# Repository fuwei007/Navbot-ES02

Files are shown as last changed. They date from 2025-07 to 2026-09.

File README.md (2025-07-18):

# Navbot-ES02 - Open Source Desktop Dual-Wheel Legged Robot

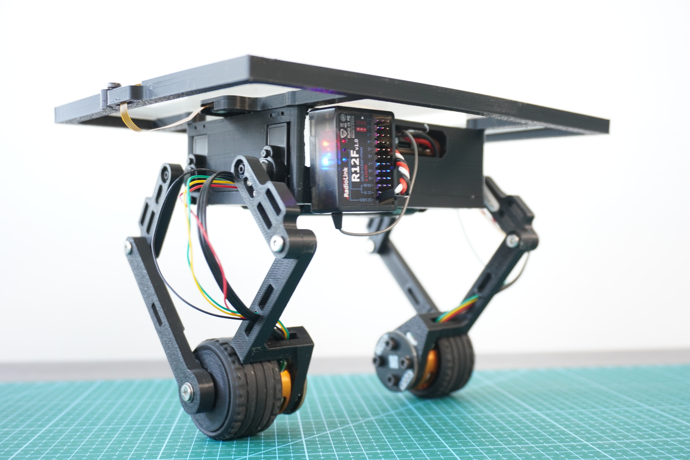
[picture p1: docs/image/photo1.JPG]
robot


**Navbot-ES02** is a compact, open-source desktop robot that combines self-balancing wheels with articulated legs. It’s an experimental platform for exploring locomotion, balance, and user interaction — ideal for makers, educators, and robotics enthusiasts.

Full tutorial: [Frank Fu’s Build Guide](https://frankfu.blog/embodied-ai-robot/diy-desktop-dual-wheel-legged-roboy/)

---

##  Key Features

-  **Self-balancing** using MPU6050 and PID control
-  **Legged motion** using 270° digital servos
-  **Touchscreen interface** for motion control to achieve  ball-balancing
-  **Radiolink T12D RC System** for real-time operation switching via PWM/SBUS.
-  **Modular Arduino-based firmware** for easy customization

---

## Hardware Overview

| Component | Description |
|---|---|
| **MCU** | ESP32-S3 DevKit |
| **Motors** |  2208 90KV 3mm Shaft Gimbal Brushless Motors |
| **IMU** |  ICM42688 a 3-axis gyroscope and a 3-axis accelerometer |
| **Servos** | Pro-Tronik PTK 7452 MG-D 2.8kg/0.11s 12.3g Micro Digital Servo |
| **HMI** | 2.8" resistive/capacitive touchscreen |
| **Battery** | 2Pcs 18650 Battery Charger Pack |
| **Controller** | Radiolink T12D 12CH 2.4G RC Transmitter R12F Receiver |

---

## 📦 Software Structure

```
Navbot-ES02/
├── OllieFOCdrive/     # Motor & balance control
├── TouchUI/           # Touchscreen-based user interface
├── WiFiControl/       # Optional WebSocket/HTML control panel
├── partitions.csv     # Flash partition layout
└── lib/               # Required Arduino libraries
```

---

## Getting Started

### 1. Install Requirements

- Arduino IDE 2.x
- ESP32 board package (`esp32@3.0.7`)
- Libraries (via Library Manager or GitHub):
  - [SimpleFOC](https://github.com/simplefoc/Arduino-FOC)
  - [SimpleFOcDrivers](https://github.com/simplefoc/Arduino-FOC-drivers)
  - [Preferences](https://github.com/vshymanskyy/Preferences)
    
### 2. Flash the Firmware

```bash
git clone https://github.com/fuwei007/Navbot-ES02.git
```

- Open `OllieFOCdrive.ino` with Arduino IDE
- Select board: `ESP32S3 Dev Module`
- Upload code and monitor via Serial for debugging

### 3. Connect the model remote control
ES02 has 3 lines, namely GND, 5V, and sbus.

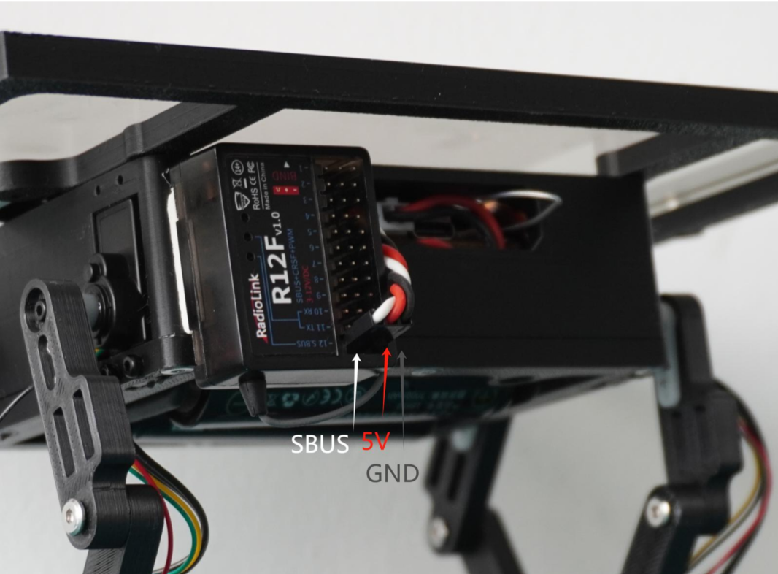
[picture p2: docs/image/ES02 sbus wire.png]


The remote control receiver may have multiple interfaces. It is necessary to confirm the sbus
output port by yourself. The following picture shows the wiring ports of the RadioLink receiver.

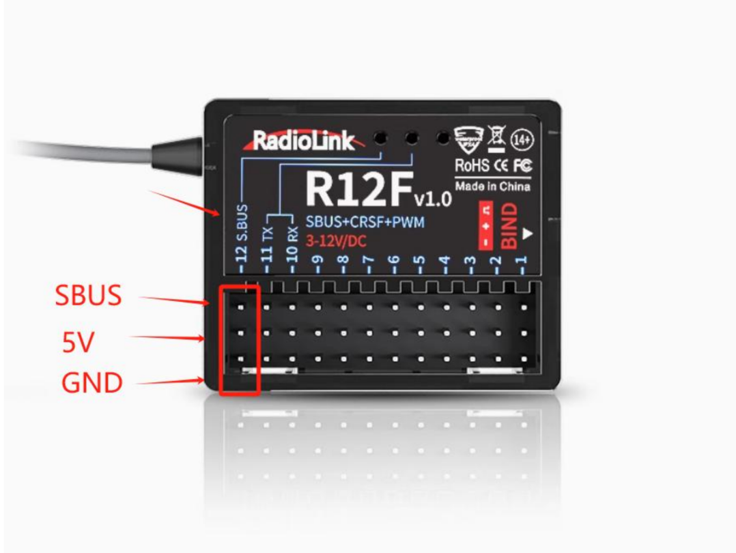
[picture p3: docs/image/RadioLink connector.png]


The channels of the joystick are generally defaulted to ch1-4. Besides, six auxiliary channels
are needed to switch on some functions. Each remote control is different, and they should be set
according to personal habits. The corresponding functions of ch6-10 can be referred to as follows:

- CH5 : 3-section switch, 0:stop, 1:start, 2:start and touch tablet enable. 
- CH6 : 2-section switch, 0:posture mode, 1:mark mode. 
- CH7 : 2-section switch, manual or auto roll, 0:manual , 1:auto . 
- CH8 : 3-section switch, 0:default, 1:pitching adjust, 2:ball poise. 
- CH9 : The x-coordinate of the small ball . 
- CH10:The y-coordinate of the small ball.

---

## Tourial Videos

- DIY ES02 Desktop dual-wheel legged bot Preview:
  
  Video 2 (https://www.youtube.com/watch?v=u7Jmyq_AXwc)

- Open Source ESP32 DIY Robot ES02: Learn Coding & Robotics | Educational Dual-Wheel Legged Bot:
  Video 1 (https://www.youtube.com/watch?v=hujr_VRSyrw)

---

## Discord link
| Link: [https://discord.gg/syywQ2CKN3](https://discord.gg/syywQ2CKN3)        |
| :------------: |
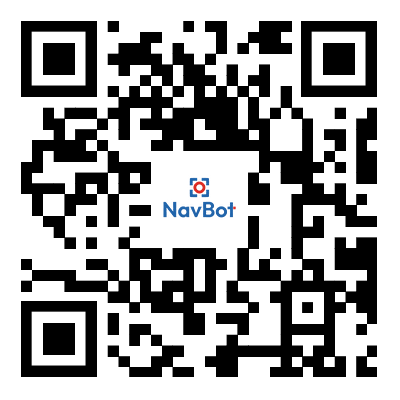
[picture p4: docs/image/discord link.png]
|  |

---

## Acknowledgments

- [SimpleFOC Community](https://simplefoc.com/)
- [Frank Fu’s Robotics Blog](https://frankfu.blog)
- [LVGL GUI Library](https://lvgl.io/)
- Arduino & ESP32 Open Source Communities

---

> Feel free to fork, contribute, or build your own version!  
> PRs and feedback are always welcome.

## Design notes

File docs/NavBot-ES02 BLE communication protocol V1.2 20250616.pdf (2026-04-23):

# NAVBOT-ES02 BLE communication protocol

Table of Contents

## Revision History

# DOCUMENT HISTORY

SOFTWARE REVISION | CHANGES MADE | REVISION DATE | EDITED BY
1.0 | First draft | 6/12/2025 | XiaoleChen
1.1 | Modify the description of the 12th byte in CMD_MANEUVER | 6/16/2025 | XiaoleChen
1.2 | Add the JSON protocol and define the key name:get_device_info | 3/30/2026 | XioaleChen

## 1. BLE information

BLE NAME :
navbot_es02-******

Service UUID:
6E400011-B5A3-F393-E0A9-E50E24DCCA9E

Send data characteristic UUID: 6E400012-B5A3-F393-E0A9-E50E24DCCA9E

Receive data characteristic UUID: 6E400013-B5A3-F393-E0A9-E50E24DCCA9E

## 2. Data frame agreement

Byte | Name | Description
Byte 1 | Header1 | Fixed 0x55
Byte 2 | Header2 | Fixed 0xAA
Byte 3 | Command | The control command of this data frame, reference 3.Command
Byte 4 | Remaining | The number of frames remaining after synthesizing the complete data,reference 4.Subcontracting
Byte 5 | Null | Retain
Byte 6 | Data
Byte 7 | Data
Byte 8 | Data
Byte 9 | Data
Byte 10 | Data
Byte 11 | Data
Byte 12 | Data
Byte 13 | Data
Byte 14 | Data
Byte 15 | Data
Byte 16 | Data
Byte 17 | Data
Byte 18 | Data
Byte 19 | Data
Byte 20 | Data

## 3. Command

The third byte is the command byte, which determines the function of the data from the 6th to the 20th byte. The current definition is as follows:
Command | Name | Explanation
0x10 | CMD_MANEUVER retain | Robot maneuver, at this time the meaning of the data frame reference 3.0.CMD_MANEUVER. 0x01
0x02 | CMD_JSON

JSON transmission, byte 6 to byte 20 represent the JSON body. Refer to 3.2. CMD_JSON

## 3.0. CMD_MANEUVER

When byte3(command) is equal to 0x00, it indicates that bytes 6 to 20 control the maneuverability of the robot. At this time, the data should follow the following rules:
Byte | Name | Description
Byte 1 | Header1 | Fixed 0x55
Byte 2 | Header2 | Fixed 0xAA
Byte 3 | Command | 0x10
Byte 4 | Remaining | 0x00
Byte 5 | Null | 0x00
Byte 6 | CH1_roll | The robot leans to the left and right. Value 100 to -100. Byte 7 | CH2_height | The height of the robot. Value 0 to 100 . Byte 8 | CH3_pitching | Move forward or backward. Value 100 to -100. Byte 9 | Ch4_yaw | The robot spin. Value 100 to -100. Byte 10 | SWA_en | 3-section switch, 0:stop, 1:start, 2:start and touch tablet
enable. Byte 11 | SWB_posture | 2-section switch, 0:posture mode, 1:mark mode. Byte 12 | SWC_roll_mode | 2-section switch, manual or auto roll, 0:manual , 1:auto . Byte 13 | SWD_posture_option | 3-section switch, 0:default, 1:pitching adjust, 2:ball poise. Byte 14 | VRA_ball_x | The x-coordinate of the small ball. Value 5 to -5. Byte 15 | VRB_ball_y | The y-coordinate of the small ball. Value 5 to -5. Byte 16 | Null | 0x00
Byte 17 | Null | 0x00
Byte 18 | Null | 0x00
Byte 19 | Null | 0x00
Byte 20 | Null | 0x00

## 3.0.1. Data frame demonstration：

55 AA 10 00 00 00 00 00 00 01 00 00 00 00 00 00 00 00 00 00
SWA_en(Byte 10) = 1, At this point, start the machine and hold it upright with your hand. Then you can stand still on the

spot. 55 AA 10 00 00 00 00 0A 00 01 00 00 00 00 00 00 00 00 00 00

SWA_en(Byte 10) | = 1, CH3_pitching(Byte 8) = 10, After standing up, the machine moved forward at a speed of 10. 55 AA 10 00 00 00 00 8A 00 01 00 00 00 00 00 00 00 00 00 00
SWA_en(Byte 10) | = 1, CH3_pitching(Byte 8) = -10, After standing up, the machine moves backward at a speed of 10. 55 AA 10 00 00 00 00 00 08 01 00 00 00 00 00 00 00 00 00 00
SWA_en(Byte 10) | = 1, Ch4_yaw(Byte 9) | = 8, After standing up, the machine rotates clockwise at an angular velocity of 8. 55 AA 10 00 00 00 00 00 88 01 00 00 00 00 00 00 00 00 00 00
SWA_en(Byte 10) | = 1, Ch4_yaw(Byte 9) | = -8, After standing up, the machine rotates counterclockwise at an angular velocity of 8. 3.1. NULL

## 3.2. CMD_JSON:

This command data frame format is:
Byte | Name | Description
Byte 1 | Header1 | Fixed 0x55
Byte 2 | Header2 | Fixed 0xAA
Byte 3 | Command | 0x02

Byte 4 | Remaining Null | * Byte 5 Idle

Byte 6 ~Byte 20
Body data JSON body,Transmission can be subcontracted. 3.2.1. JSON protocol :

Using the key name "type" to distinguish different commands, the currently defined values for the "type" key are as follows:
Type value：(string) | explain
“get_device_info” | Obtain robot information, refer to 3.2.1.1 get_device_info

## 3.2.1.1. get_device_info

The upper computer sends:
{ “type”:”get_device_info”

}
Robot reply:
{ | “type”: | “get_device_info”, “battery_level”: | double, “battery_voltage”: double, }

## 4. Subcontracting

The number of frames remaining after synthesizing the complete data;The size of one frame of data is 20 bytes. Excluding the 5-byte header, the user can still use 15 bytes. However, when using commands such as JSON, these 15 bytes are clearly insufficient for use. Therefore, the 4th byte of each frame data can be used to indicate how many more frames of data are to

be processed together. For example, if the data to be sent now consists of 32 bytes, the data format would be as follows (xx represents the actual data):

### 55 AA xx 02 00 xx xx xx xx xx xx xx xx xx xx xx xx xx xx xx 55 AA xx 01 00 xx xx xx xx xx xx xx xx xx xx xx xx xx xx xx 55 AA xx 00 00 xx xx xx xx xx xx xx xx xx xx xx xx xx xx xx

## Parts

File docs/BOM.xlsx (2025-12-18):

Category | Component | linkS | Specification | Quantity | Description
Hardware | Flanged Bearing | https://www.amazon.com/XIKE-Bearings-3x6x2-5mm-Pre-Lubricated-Selectric/dp/B0D2KYP9JD | 3×6×2.5 mm | 2 | Rod L2
 | Bearing | https://www.amazon.com/uxcell-6701-2RS-Groove-Bearings-Double/dp/B082PQ8DC2 | 12×18×4 mm | 2 | Wheel Hub
 | Hex Socket Screw | https://www.amazon.com/Fgruh-750PCS-Assortment-Washers-Assorted/dp/B0FGV5FCBN?sp_csd=d2lkZ2V0TmFtZT1zcF9hdGY | M3×6 | 2 | Wheel Hub to Rod L2
 | Hex Socket Screw |  | M3×10 | 8 | Motor to Encoder
 | Hex Socket Screw | https://www.amazon.com/Fgruh-1200PCS-Assortment-Washers-Assorted/dp/B0FGV5K8BT?sp_csd=d2lkZ2V0TmFtZT1zcF9hdGY | M2×8 | 4 | Servo to Servo Arm
 | Hex Socket Screw |  | M2×6 | 6 | Wheel Hub to Motor
 | Hex Locking Screw & Nut | https://detail.tmall.com/item.htm?ali_trackid=318_23a26b5b4c76f7f8a2ef9837f0edb194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 | M2×12 (Set) | 8 | Lower Arm to Upper Arm
 | Hex Socket Self-tapping Screw | https://www.amazon.com/Metric-Tapping-Stainless-Assortment-Drilling/dp/B0D1R21JRR | M3×5 | 6 | Mainboard to Bracket ×4 / Touchscreen to Stand ×2
 | Countersunk Hex Self-tapping Screw |  | M3×6 | 2 | Battery Holder
 | Countersunk Hex Self-tapping Screw |  | M3×10 | 12 | Base to Bracket ×4 / Base to Top Cover ×4 / Top Cover to Touchscreen Stand ×4
 | Countersunk Hex Self-tapping Screw |  | M3×18 | 12 | Rod L5 / Rod L6
 | Hex Socket Self-tapping Screw | https://www.amazon.com/Whitewashed-Self-Tapping-Hexagonal-Self-Drilling-Fasteners/dp/B0F1JYTY33 | M1.7×6 | 8 | Servo Arm to Rod L1
 | Hex Socket Self-tapping Screw | https://www.amazon.com/Whitewashed-Self-Tapping-Hexagonal-Self-Drilling-Fasteners/dp/B0F1JYKM64 | M1.7×10 | 8 | Servo to Base
 | Steel Ball (Diameter) | // | 22 mm | 1 | Used for top ball support
Wires | SH1.0 Cable | jLhkiMjvlWzf20CDxy2JfJ4Jcx6Da1d6_YxCGVCAp2FeKimA2qR2AeveBVZlwNlAqCN59ZZSTGm0iPQm9QxrrhbzW8yj_p5FoFC0xtJEouJcRDbRKffhAhPzKMzW5XBSkb6nk7JZq8_URwwl9zUZRra7onyzfd1nP7ulprgyJr7Y40WYrsKdRTsBeodiVKbwYnfKO1gHhlIl8zZwIQNvCrqvjZLzNFy9HY3i_j13vM2EiAD5jhJBrvSYUlat2Xb1bodeY7x2JP6XTelKuG9nJ0bqOmzMA | 200 mm, reverse connection | 3 | 2 Encoders / Communication between two units
 | SH1.0 Cable |  | 100 mm, reverse connection | 1 | Touchscreen control board to mainboard
 | Dupont Cable | https://www.amazon.com/Kidisoii-Dupont-Connector-Pre-Crimped-3P-30CM/dp/B0CCTXZW3D | 3PIN × 10 cm | 1 | To SUBS receiver
Electronics | Encoder Module | // | AS5600 | 2
 | Mini quadruped mainboard | // |  | 1
 | Resistive Touchscreen | https://item.taobao.com/item.htm?app=chrome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 | 181×139 mm | 1
 | 4-wire Resistive Touchscreen Driver | // | Serial TTL level | 1
 | ICM42688P Module | // |  | 1
 | Tire Rubber | https://www.amazon.com/Shaluoman-Soft-Rubber-Tires-Tyre/dp/B07F8Q4BHJ | 37×22 mm (outer diameter × width) | 2
 | Servo | https://item.taobao.com/item.htm?id=534087183869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 | GX-S7445 | 4
 | Brushless Motor | https://www.amazon.com/Gimbal-Brushless-100-200g-Gopro3-Quadcopter/dp/B0FM8JYT38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 | 2208-90kv | 2
 | 18650 Battery Holder | https://www.amazon.com/DAIERTEK-18650-Battery-Holder-Total/dp/B0BG3YLCFD?sp_csd=d2lkZ2V0TmFtZT1zcF9hdGY | 2S battery holder | 1
 | Radial Magnet | https://www.amazon.com/GXHUANG-6x1-5mm-Decorative-Refrigerator-Projects/dp/B0DHQ7FY14 | 6×1.5 mm | 2
 | Remote + Receiver Set | https://www.amazon.com/Radiolink-T12D-Transmitter-Telemetry-Long-Range/dp/B0DB5JHSS6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 | T12D | 1 | Ten control channels are required.
 | 18650 Battery | https://www.amazon.com/MC-ELIN-Rechargeable-Batteries-Flashlights-Headlamps/dp/B0FSQT6BMF |  | 2
3D Printed Parts | loamcake |  |  | 1 | Top Cover
 | lowercover |  |  | 1 | Base
 | magnetsleeve |  |  | 2 | Magnet Sleeve
 | motherboardbracket |  |  | 1 | Mainboard Bracket
 | pole1 |  |  | 2 | Rod L1
 | pole2 |  |  | 2 | Rod L1
 | pole3 |  |  | 2 | Rod L2
 | pole4 |  |  | 2 | Rod L2
 | pole5 |  |  | 2 | Rod L5 (for two-unit connection)
 | pole6 |  |  | 2 | Rod L6 (for two-unit connection)
 | wheelHub |  |  | 2 | Wheel Hub
 | touchscreenstand |  |  | 1 | Touchscreen Bracket

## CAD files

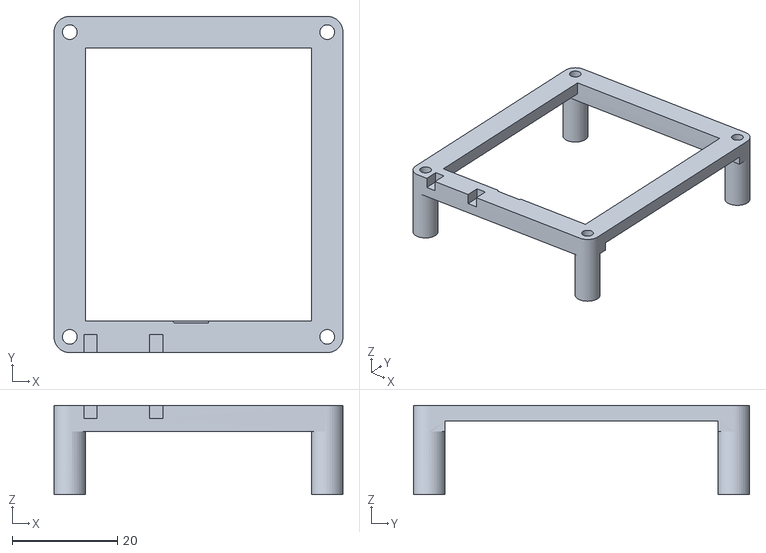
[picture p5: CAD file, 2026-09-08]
hardware/3d print/motherboardbracket_hollow.stl
55.0 x 64.0 x 17.0

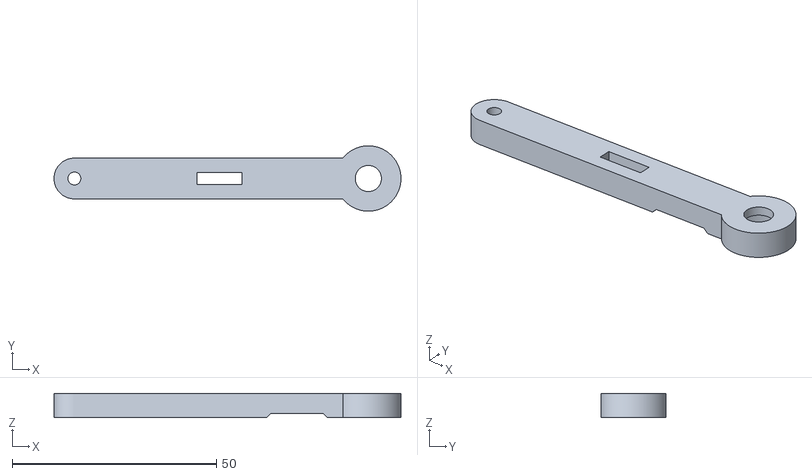
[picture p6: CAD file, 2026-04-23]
hardware/3d print/Calf_Outside.stl
85.0 x 16.0 x 6.00

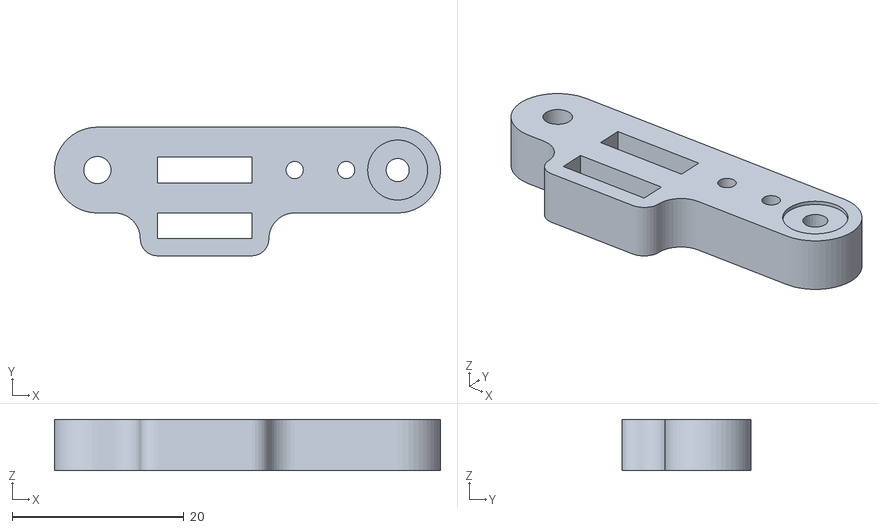
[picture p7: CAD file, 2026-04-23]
hardware/3d print/Thigh_R.stl
45.0 x 15.0 x 6.00

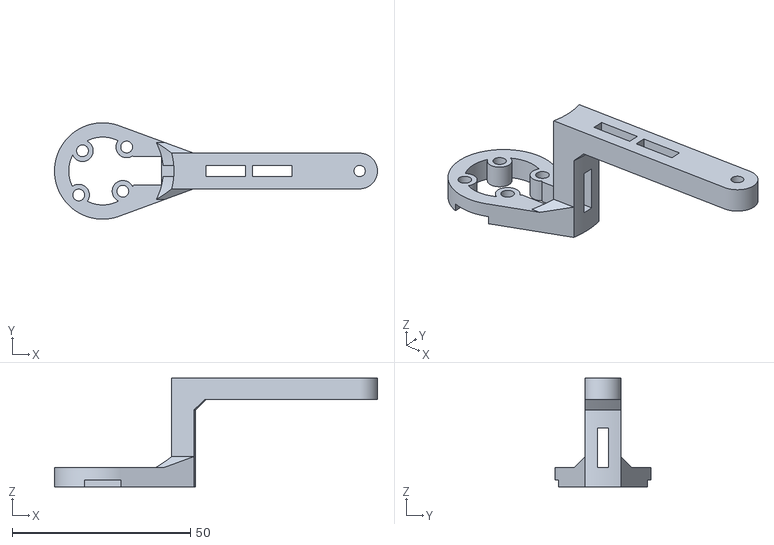
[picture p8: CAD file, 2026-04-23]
hardware/3d print/Calf_Inside.stl
90.5 x 27.0 x 30.5

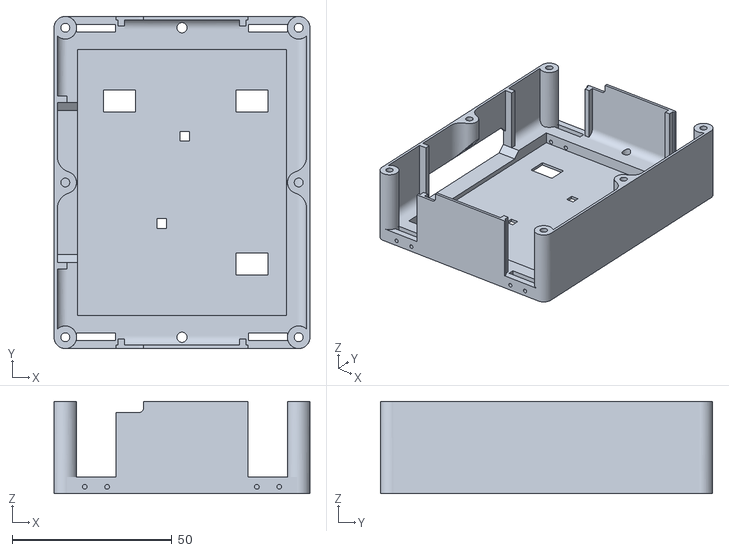
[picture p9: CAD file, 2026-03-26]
hardware/3d print/loamcake.stl
80.1 x 103.9 x 28.8

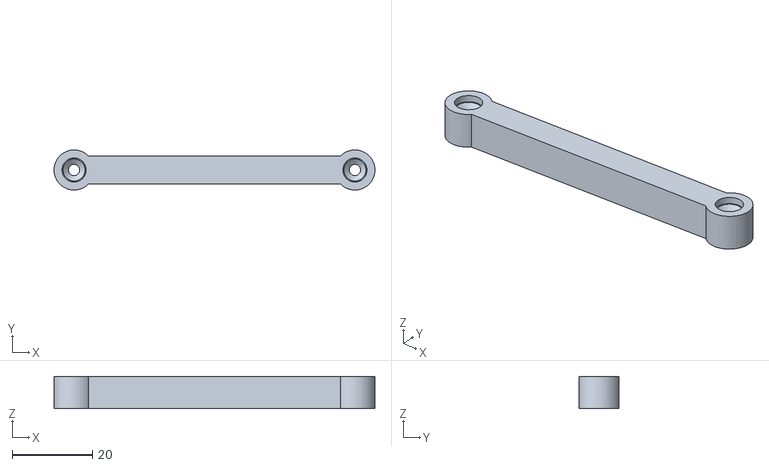
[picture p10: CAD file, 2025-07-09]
hardware/3d print/pole6.stl
80.0 x 9.99 x 8.00

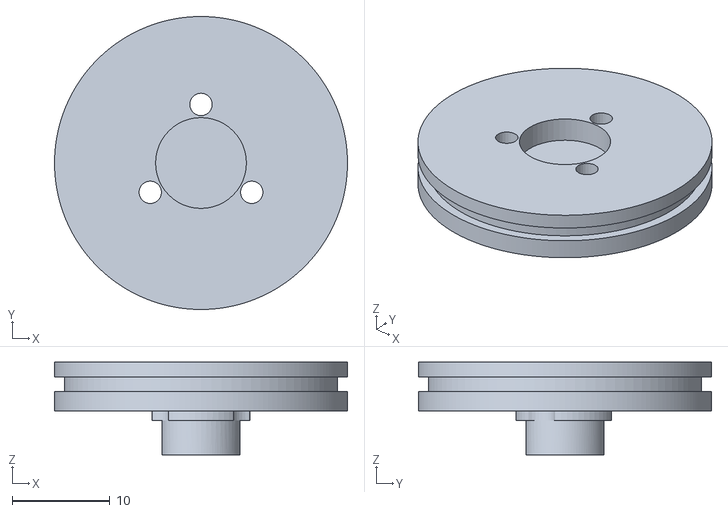
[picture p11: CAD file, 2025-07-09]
hardware/3d print/Wheel_Hub.stl
30.0 x 30.0 x 9.50

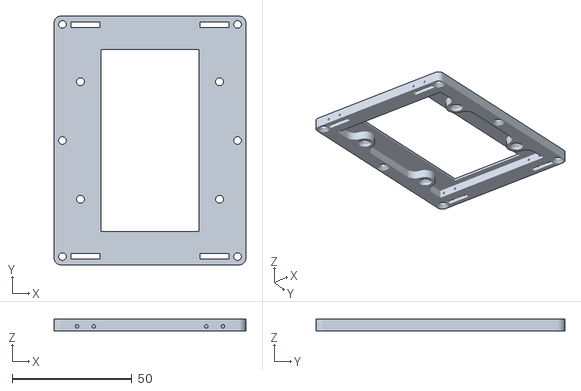
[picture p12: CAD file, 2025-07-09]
hardware/3d print/lowercover.stl
80.0 x 103.8 x 5.00

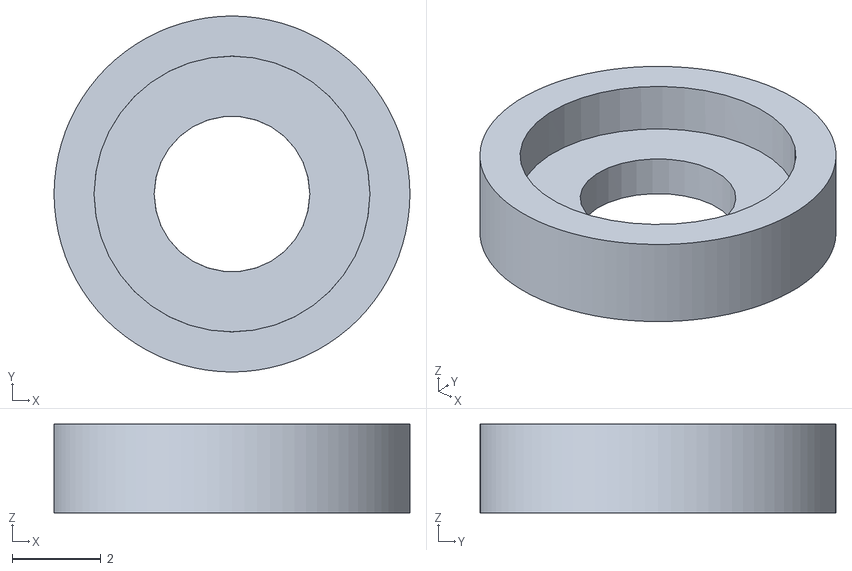
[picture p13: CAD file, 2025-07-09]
hardware/3d print/magnetsleeve.stl
8.00 x 8.00 x 2.00

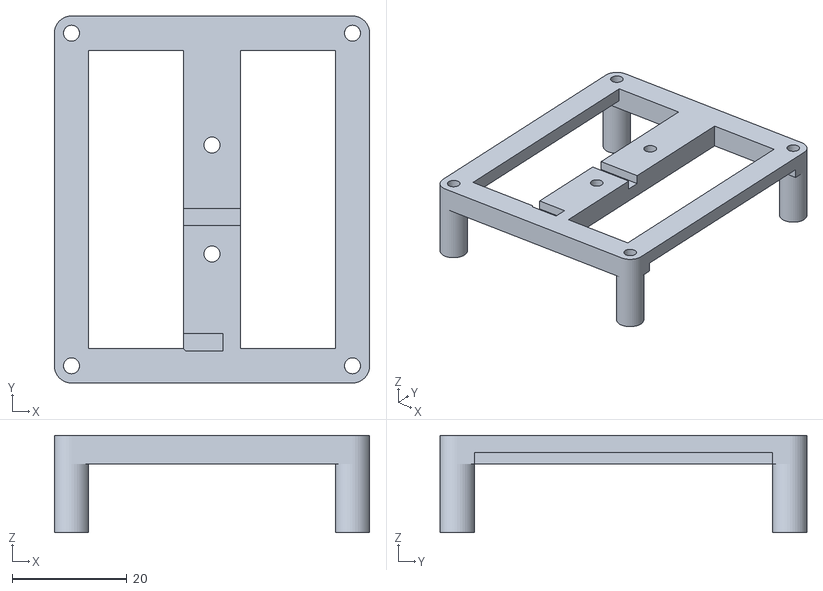
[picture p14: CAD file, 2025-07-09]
hardware/3d print/motherboardbracket.stl
55.0 x 64.0 x 17.0

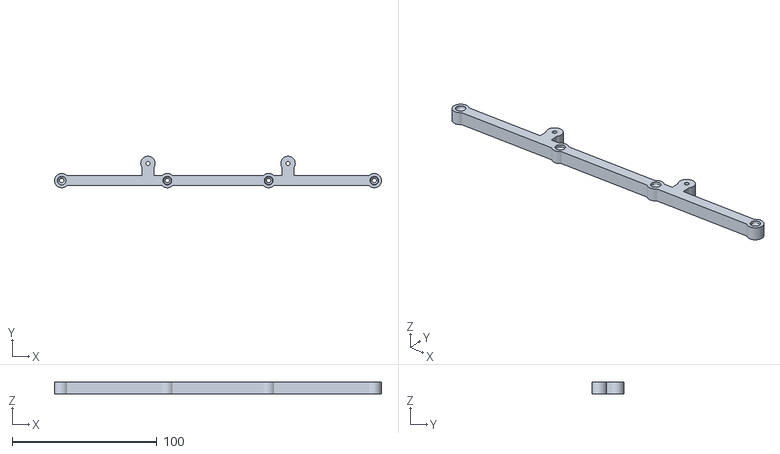
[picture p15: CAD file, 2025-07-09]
hardware/3d print/pole5.stl
226.0 x 21.9 x 8.00

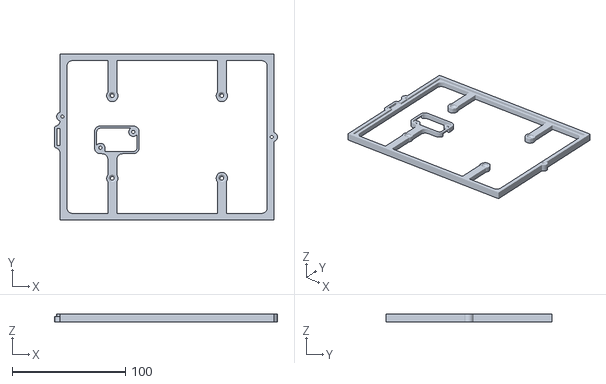
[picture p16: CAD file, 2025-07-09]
hardware/3d print/touchscreenstand.stl
197.1 x 147.0 x 7.00

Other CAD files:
hardware/3d print/Thigh_L.stl

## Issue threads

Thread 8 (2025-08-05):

Temperature collection anomaly

nullhat2, 2025-08-05:
The temperature collection method is abnormal, resulting in compilation failure.

Closed 2025-08-08.

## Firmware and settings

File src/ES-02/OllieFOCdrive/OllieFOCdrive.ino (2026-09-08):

#include <Arduino.h>
#include <SimpleFOC.h>
#include <Preferences.h>  // This library is used for key-value data storage and retrieval in ESP32, enabling data persistence
#include "SlotCalibration.h"
#include "FUTABA_SBUS.h"
#include "ServoControl.h"
#include "ICM42688.h"
#include "MahonyFilter.h"
#include "OllieFOCdrive.h"
#include "filter.h"
#include "touchscreen.h"
#include "ble.h"
#include "robot.h"


// commander communication instance
Commander command = Commander(Serial);

// ----- Editable Constants
#define SensorSwitch SENSOR_SWITCH_IIC_AS5600                                // 1: SPI  2: IIC AS5600
#define Communication_object COMMUNICATION_OBJECT_TWO_OR_FOUR_WHEEL_BALANCE  // 0: 2-wheel balance || 4-wheel balance movement  1: simpleFOC Studio host computer  2: control dual motors  3: sample torque data
#define TorqueCompensation TORQUE_COMPENSATION_OFF                           // 1: torque compensation  0: no torque compensation (cannot be modified)
#define SwitchUser SWITCH_USER_MODE_SPEED_MODE                               // 0: view encoder position and direction  1: sample motor 1 torque compensation data  2: sample motor 2 torque compensation data  3: torque  4: speed  5: angle mode
#define CurrentUser CURRENT_LOOP_OFF                                         // 1: enable current loop
#define M2CurrentUser CURRENT_LOOP_OFF                                       // 1: enable current loop for motor 2

#define AdjusParameter ADJUST_BALANCE_SPEED_YAW_ROLL        // 0: balance, speed, yaw, roll parameter tuning   1: ball pushing
#define SwitchingPattern SWITCHING_PATTERN_TWO_WHEEL_MODE   // 0: two-wheel  1: four-wheel  switching mode
#define MasterSlaveSelection MASTER_SLAVE_SELECTION_MASTER  // 0: slave   1: master

//      Two-Wheel PID Gains for Remote Control Mode (Without Touchscreen)
#define PID_ROLL_P_NO_TOUCH 0.06
#define PID_ROLL_I_NO_TOUCH 1.5
#define PID_ROLL_D_NO_TOUCH 0.0028
#define PID_ROLL_LIMIT_NO_TOUCH 2
#define PID_SPEED_P_NO_TOUCH 0.3
#define PID_SPEED_I_NO_TOUCH 0.3
#define PID_SPEED_D_NO_TOUCH 0
#define PID_SPEED_LIMIT_NO_TOUCH 50
#define PID_ANGLE_P_NO_TOUCH 66
#define PID_ANGLE_I_NO_TOUCH 222  // if stuttering/shaking when balancing, consider reducing this Integral value (ex. 165 instead of 222)
#define PID_ANGLE_D_NO_TOUCH 1
#define PID_ANGLE_LIMIT_NO_TOUCH 0.1

//      Two-Wheel PID Gains for Remote Control Mode (With Touchscreen)
#define PID_ROLL_P_WITH_TOUCH 0.08
#define PID_ROLL_I_WITH_TOUCH 1.5
#define PID_ROLL_D_WITH_TOUCH 0.005
#define PID_ROLL_LIMIT_WITH_TOUCH 2
#define PID_SPEED_P_WITH_TOUCH 0.12
#define PID_SPEED_I_WITH_TOUCH 0.12
#define PID_SPEED_D_WITH_TOUCH 0
#define PID_SPEED_LIMIT_WITH_TOUCH 50
#define PID_ANGLE_P_WITH_TOUCH 9
#define PID_ANGLE_I_WITH_TOUCH 222
#define PID_ANGLE_D_WITH_TOUCH 0.11
#define PID_ANGLE_LIMIT_WITH_TOUCH 0.1

#define IMU_SAMPLING_RATE_HZ 1000.0f  // Sampling frequency
#define IMU_LPF_CUTOFF_FREQ_HZ 50.0f  // Cutoff frequency for low-pass filter
#define IMU_CALL_COUNT 100            // Number of times the function is called

#define BODY_THIGH_LENGTH_M 0.035f  // Thigh length (m)
#define BODY_SHANK_LENGTH_M 0.072f  // Shank length (m)

#define BOARD_PIN_LED 35        // LED IO
#define BOARD_PIN_ANALOG_IN 17  // Battery voltage IO

#define IMU_ACCEL_RANGE_G 8.0              // Unit: g
#define IMU_GYRO_RANGE_DEG_PER_SEC 2000.0  // Unit: °/s

#define CUSTOM_SERVO_1_PIN 11
#define CUSTOM_SERVO_2_PIN 12
#define CUSTOM_SERVO_3_PIN 21
#define CUSTOM_SERVO_4_PIN 14

#define CURRENT_SENSOR_MV_PER_AMP 90.0f  // ACS712-05B sensitivity is 185mV/A

#define SBUS_CHANNEL_MAX 1792
#define SBUS_CHANNEL_MIN 192

#define SERIAL_PACKET_HEADER_BYTE_1 12
#define SERIAL_PACKET_HEADER_BYTE_2 34
#define SERIAL_PACKET_END_BYTE 0
#define SERIAL_BAUD_RATE 2000000
// -------------------------------------

// Body
float TargetLegLength = 0;          // Target leg length
float LegLength = 0.06f;            // Leg length
float BarycenterX = 0;              // Center of mass X
float BodyPitching = 0;             // Pitch
float BodyRoll = 0;                 // Roll
float MovementSpeed = 0;            // Movement speed
float BodyTurn = 0;                 // Turning
float SlideStep = 0;                // Slide step
float BodyX = 0;                    // X position (controller output)
int RobotTumble = ROBOT_TUMBLE_NO;  // Robot tumble (fall detection)

body_t body;

// 滤波
float LegLength_f = 0.06f;     // Leg length
float BarycenterX_f = 0;       // Center of mass X
float BodyPitching_f = 0;      // Pitch
float BodyRoll_f = 0;          // Roll
float MovementSpeed_f = 0;     // Movement speed
float BodyTurn_f = 0;          // Turning
float SlideStep_f = 0;         // Slide step
float BodyX_f = 0;             // X position
biquadFilter_t FilterLPF[15];  // Second-order low-pass filter
float TouchY_Pid_outputF = 0;
float TouchX_Pid_outputF = 0;

float cutoffFreq = 200;
float enableDFilter = 1;
float LpfOut[6];  //

void CutoffFreq(char *cmd) {
  command.scalar(&cutoffFreq, cmd);
}

void EnableDFilter(char *cmd) {
  command.scalar(&enableDFilter, cmd);
}

int LED_HL = 1;
int LED_count = 0;
int LED_dt = 100;
int sensorValue = 0;              // value read from the pot
biquadFilter_t VoltageFilterLPF;  // Second-order low-pass filter
uint16_t VoltageADC = 0;          // Battery voltage ADC data
float VoltageADCf = 0;            // Battery voltage ADC data
float Voltage = 0;                // Battery voltage

// IMU
//  Create MahonyFilter object, set proportional gain and integral gain
MahonyFilter mahonyFilter(0.4f, 0.001f);
// Accelerometer range (here set to ±8g)
// Gyroscope range (here assumed to be ±2000°/s)
attitude_t attitude;
float roll_ok;   //
float pitch_ok;  //

zeroBias_t zeroBias;  // Zero offset
unsigned long timestamp_prev = 0;
float IMUtime_dt = 0;

/* Low-pass filter parameters */
float RATE_HZ_last = IMU_SAMPLING_RATE_HZ;            // Sampling frequency
float LPF_CUTOFF_FREQ_last = IMU_LPF_CUTOFF_FREQ_HZ;  // Cutoff frequency

float RATE_HZ = IMU_SAMPLING_RATE_HZ;            // Sampling frequency
float LPF_CUTOFF_FREQ = IMU_LPF_CUTOFF_FREQ_HZ;  // Cutoff frequency
biquadFilter_t ImuFilterLPF[6];                  // Second-order low-pass filter

void ImuRATE_HZ(char *cmd) {
  command.scalar(&RATE_HZ, cmd);
}
void ImuLPF_CUTOFF_FREQ(char *cmd) {
  command.scalar(&LPF_CUTOFF_FREQ, cmd);
}

void Target_Leg_Length(char *cmd) {
  command.scalar(&TargetLegLength, cmd);
}

// Complementary filter
float angleGyroX, angleGyroY, angleGyroZ,
  angleAccX, angleAccY;
float angleX, angleY, angleZ;
float accCoef = 0.02f;
float gyroCoef = 0.98f;

//  Declare a Preferences object for subsequent read/write operations to flash memory
Preferences preferences;
//  Define a floating-point array to store Euler angle data
float zeroBiasFlash[9];
//  Define a character string pointer array to store the keys corresponding to the roll and pitch angles, which can be directly modified by the user
//  The key name is used to uniquely identify data in flash memory
const char *zeroBiasKeys[9] = {
  "roll",
  "pitch",
  "gyroX",
  "gyroY",
  "gyroZ",
  "servoAngle1",
  "servoAngle2",
  "servoAngle3",
  "servoAngle4"
};

int IMUCallCounter = 0;  //  Call counter

// Servo
void zeroBias_servo1(char *cmd) {
  command.scalar(&zeroBias.servo1, cmd);
}
void zeroBias_servo2(char *cmd) {
  command.scalar(&zeroBias.servo2, cmd);
}
void zeroBias_servo3(char *cmd) {
  command.scalar(&zeroBias.servo3, cmd);
}
void zeroBias_servo4(char *cmd) {
  command.scalar(&zeroBias.servo4, cmd);
}

bool pid_gains_mode_is_enabled(int mode) {
  return (mode == REMOTE_CONTROL_PID_GAINS_MODE_ON_WITHOUT_TOUCH || mode == REMOTE_CONTROL_PID_GAINS_MODE_ON_WITH_TOUCH);
}

//  Create ServoControl object, pass in the custom pin
ServoControl servoControl(CUSTOM_SERVO_1_PIN, CUSTOM_SERVO_2_PIN, CUSTOM_SERVO_3_PIN, CUSTOM_SERVO_4_PIN);

// Remote control
FUTABA_SBUS sBus;
float sbuschx[8] = { 0 };
int sbus_dt_ms = 0;
int pid_gains_mode = REMOTE_CONTROL_PID_GAINS_MODE_OFF;
int posture_or_mark_mode = REMOTE_CONTROL_PM_POSTURE_MODE;
int roll_mode = REMOTE_CONTROL_ROLL_MODE_MANUAL;
int attitude_mode = REMOTE_CONTROL_ATTITUDE_MODE_DEFAULT;
float top_ball_x = 0;
float top_ball_y = 0;
float sbus_top_ball_x_smoothed = 0;
float sbus_top_ball_y_smoothed = 0;

//  Create PID controller instance
float Select = 0;             // Select the data to print
float CalibrationSelect = 0;  // Save calibration data 0: Calibration end  1: Calibrate gyroscope  2: Calibrate Euler angle  3: Calibrate servo

float PidParameterTuning = 0;  // 0: Disable parameter tuning  1: Enable parameter tuning

PIDController AnglePid(0, 0, 0, 0, 0);          // 4 22 0.08   (Kp, Ki, Kd ,ramp ,limit)
PIDController SpeedPid(0.1, 0.1, 0, 0, 50);     //
PIDController YawPid(11, 33, 0, 0, 0);          //
PIDController RollPid(0.06, 1.5, 0.003, 0, 2);  //
PIDController TouchXPid(0.2, 0, 0.04, 0, 0);    //
PIDController TouchYPid(0.2, 0, 0.08, 0, 0);    //

float control_torque_compensation = 0;  // Control torque compensation

float PidDt = 0.01;

//  Create MyPIDController instance, set initial parameters
MyPIDController Angle_Pid(0, 0, 0, 0, 0, PidDt, 0, 0);  // p i d iLimit outputLimit dt EnableDFilter cutoffFreq
MyPIDController Speed_Pid(0, 0, 0, 0, 0, PidDt, 0, 0);
MyPIDController Yaw_Pid(0, 0, 0, 0, 0, PidDt, 0, 0);
MyPIDController Roll_Pid(0, 0, 0, 0, 0, PidDt, 0, 0);
MyPIDController Pitching_Pid(0, 0, 0, 0, 0, PidDt, 0, 0);

MyPIDController TouchX_Pid(0, 0, 0, 0, 10, PidDt, 0, 0);
MyPIDController TouchY_Pid(0, 0, 0, 0, 8, PidDt, 0, 0);

void ControlTorqueCompensation(char *cmd) {
  command.scalar(&control_torque_compensation, cmd);
}

void Pid_Parameter_Tuning(char *cmd) {
  command.scalar(&PidParameterTuning, cmd);
}
void User_command(char *cmd) {
  if (*cmd == '{') {
    rp.json_test(cmd);
  }else{
    Pid_Parameter_Tuning(cmd);
  }
}

void TwoKp(char *cmd) {
  command.scalar(&mahonyFilter.twoKp, cmd);
}
void TwoKi(char *cmd) {
  command.scalar(&mahonyFilter.twoKi, cmd);
}

void KeyScalar(char *cmd) {
  command.scalar(&Select, cmd);
}
void KeyCalibration(char *cmd) {
  command.scalar(&CalibrationSelect, cmd);
}

#if AdjusParameter == ADJUST_BALANCE_SPEED_YAW_ROLL
void CbAnglePid(char *cmd) {
  command.pid(&AnglePid, cmd);
}
void CbSpeedPid(char *cmd) {
  command.pid(&SpeedPid, cmd);
}
void CbYawPid(char *cmd) {
  command.pid(&YawPid, cmd);
}

void CbRollPid(char *cmd) {
  command.pid(&RollPid, cmd);
}

#elif AdjusParameter == ADJUST_BALL_PUSHING

void CbTouchXPid(char *cmd) {
  command.pid(&TouchXPid, cmd);
}

void CbTouchYPid(char *cmd) {
  command.pid(&TouchYPid, cmd);
}
#endif

float Motor1_voltage_compensation = 0;
float Motor2_voltage_compensation = 0;
double Motor1_place_last = 0;
float Motor1_Velocity = 0;
float Motor1_Velocity_f = 0;
LowPassFilter Motor1_Velocity_filter = LowPassFilter(0.01);  // Tf = 10ms

double Motor2_place_last = 0;
float Motor2_Velocity = 0;
float Motor2_Velocity_f = 0;
LowPassFilter Motor2_Velocity_filter = LowPassFilter(0.01);  // Tf = 10ms

Serial_t serial1;
Serial_t serial2;

float Motor1_Target = 0;
float Motor2_Target = 0;

double RightMotorAngle = 0;
double LeftMotorAngle = 0;

float time_dt = 0;
unsigned long now_us = 0;
unsigned long now_us1 = 0;
unsigned long now_us2 = 0;
// BLDC motor & driver instance
BLDCMotor motor1 = BLDCMotor(7);  // Motor pole pairs
BLDCDriver3PWM driver = BLDCDriver3PWM(15, 7, 6, 16);

BLDCMotor motor2 = BLDCMotor(7);
BLDCDriver3PWM driver2 = BLDCDriver3PWM(40, 39, 38, 37);

#if SensorSwitch == SENSOR_SWITCH_SPI
// MagneticSensorSPI(int cs, float _cpr, int _angle_register)
// config           - SPI config
//  cs              - SPI chip select pin
MagneticSensorSPI sensor1 = MagneticSensorSPI(AS5147_SPI, 19);
MagneticSensorSPI sensor2 = MagneticSensorSPI(AS5147_SPI, 23);
// these are valid pins (mosi, miso, sclk) for 2nd SPI bus on storm32 board (stm32f107rc)
SPIClass *hspi = NULL;

#elif SensorSwitch == SENSOR_SWITCH_IIC_AS5600
MagneticSensorI2C sensor2 = MagneticSensorI2C(AS5600_I2C);
MagneticSensorI2C sensor1 = MagneticSensorI2C(AS5600_I2C);
TwoWire I2Cone = TwoWire(0);
TwoWire I2Ctwo = TwoWire(1);

#endif

#if CurrentUser == CURRENT_LOOP_ON
// inline current sensor instance
// ACS712-05B has the resolution of 0.185mV per Amp
InlineCurrentSense current_sense1 = InlineCurrentSense(CURRENT_SENSOR_MV_PER_AMP, 18, 17);
#endif

#if M2CurrentUser == CURRENT_LOOP_ON
// inline current sensor instance
// ACS712-05B has the resolution of 0.185mV per Amp
InlineCurrentSense current_sense2 = InlineCurrentSense(CURRENT_SENSOR_MV_PER_AMP, 35, 36);
#endif

void doMotion1(char *cmd) {
  command.motion(&motor1, cmd);
}
void doMotor1(char *cmd) {
  command.motor(&motor1, cmd);
}

void doMotion2(char *cmd) {
  command.motion(&motor2, cmd);
}
void doMotor2(char *cmd) {
  command.motor(&motor2, cmd);
}
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
void loop() {
  now_us = micros();
  // now_us2 = micros();

  // iterative function setting the outter loop target

  if (Communication_object == COMMUNICATION_OBJECT_SIMPLEFOC_STUDIO) {
    motor1.monitor();  // When using the simpleFOC Studio upper computer, this sentence must be opened. But it will affect the program execution speed
  } else if (Communication_object == COMMUNICATION_OBJECT_CONTROL_DUAL_MOTORS) {
    motor2.target = motor1.target;
  }

  motor1.move();
  motor2.move();

  // Torque compensation
  float indexF = sensor1.getMechanicalAngle() / AngleResolutionRatio;
  int index = round(indexF);
  if ((TorqueCompensation == TORQUE_COMPENSATION_ON) && (SwitchUser != SWITCH_USER_MODE_SAMPLE_TORQUE_M1) && (SwitchUser != SWITCH_USER_MODE_SAMPLE_TORQUE_M2)) {
    motor1.current_sp = motor1.current_sp + Motor1_Current_sp_data[index];
  }

  indexF = sensor2.getMechanicalAngle() / AngleResolutionRatio;
  index = round(indexF);
  if ((TorqueCompensation == TORQUE_COMPENSATION_ON) && (SwitchUser != SWITCH_USER_MODE_SAMPLE_TORQUE_M1) && (SwitchUser != SWITCH_USER_MODE_SAMPLE_TORQUE_M2)) {
    motor2.current_sp = motor2.current_sp + Motor2_Current_sp_data[index];
  }

  // iterative setting FOC phase voltage
  motor1.loopFOC();
  motor2.loopFOC();

  // Serial.print(Motor2_voltage_compensation,6);
  // Serial.print("\t");
  // Serial.println(motor2.voltage.q+Motor2_voltage_compensation,6);

  RightMotorAngle = -sensor1.getPreciseAngle();
  LeftMotorAngle = sensor2.getPreciseAngle();

  // user communication
  command.run();

  if (MasterSlaveSelection == MASTER_SLAVE_SELECTION_MASTER) {
    ImuUpdate();  // Update IMU data
    CtrlInput();  // BLE or remote control input
    RXsbus();
  }

  if ((SwitchingPattern == SWITCHING_PATTERN_TWO_WHEEL_MODE) || (MasterSlaveSelection == MASTER_SLAVE_SELECTION_SLAVE))  // Two-wheel or slave mode
    ReadTouchDat();

  time_dt = (now_us - now_us1) / 1000000.0f;
  if (time_dt >= 0.001f) {   //1kHz
    static int Serial1_count = 0;
    Serial1_count++;
    if (Serial1_count >= 5) {
      Serial1_count = 0;
      body.Serial1HZ = body.Serial1count * 40;
      body.Serial1count = 0;
    }

    if (SwitchingPattern == SWITCHING_PATTERN_FOUR_WHEEL_MODE)  // 4-wheel mode
      MotorOperatingMode();

    if ((MasterSlaveSelection == MASTER_SLAVE_SELECTION_SLAVE) && (SwitchingPattern == SWITCHING_PATTERN_FOUR_WHEEL_MODE))  // Slave && 4-wheel mode
      Read_Serial2();
    else if ((MasterSlaveSelection == MASTER_SLAVE_SELECTION_MASTER) && (SwitchingPattern == SWITCHING_PATTERN_FOUR_WHEEL_MODE))  // Host && 4-wheel mode
      Read_Serial1();

    if ((MasterSlaveSelection == MASTER_SLAVE_SELECTION_SLAVE) || (SwitchingPattern == SWITCHING_PATTERN_TWO_WHEEL_MODE))  // Slave || 2-wheel mode
      TouchBiquadFilter();                                                                                                 // Touch screen filter

    RemoteControlFiltering();  // Remote control signal filtering
    ReadVoltage();             // Battery
    print_data();              // Serial port data printing

    if (SwitchingPattern == SWITCHING_PATTERN_TWO_WHEEL_MODE)  // 2-wheel mode
      Robot_Tumble();                                          // Machine fall detection
    LED_count++;
    if (LED_count >= LED_dt) {
      // Serial.print(LED_HL);
      // Serial.println(" LED:");
      LED_count = 0;
      if (LED_HL == 1) {
        digitalWrite(BOARD_PIN_LED, LOW);  // On
        LED_HL = 0;
      } else {
        digitalWrite(BOARD_PIN_LED, HIGH);  // Off
        LED_HL = 1;
      }
    }

    if (Voltage <= 7.4)
      LED_dt = 20;
    else
      LED_dt = 100;

    if (RATE_HZ != RATE_HZ_last) {
      // Initialize second-order low-pass filter
      for (int axis = 0; axis < 6; axis++) {
        biquadFilterInitLPF(&ImuFilterLPF[axis], (unsigned int)LPF_CUTOFF_FREQ, (unsigned int)RATE_HZ);
      }
      Serial.print(" RATE_HZ:");
      Serial.print(RATE_HZ);
      RATE_HZ_last = RATE_HZ;
    }
    if (LPF_CUTOFF_FREQ != LPF_CUTOFF_FREQ_last) {
      // Initialize second-order low-pass filter
      for (int axis = 0; axis < 6; axis++) {
        biquadFilterInitLPF(&ImuFilterLPF[axis], (unsigned int)LPF_CUTOFF_FREQ, (unsigned int)RATE_HZ);
      }
      Serial.print(" LPF_CUTOFF_FREQ:");
      Serial.print(LPF_CUTOFF_FREQ);
      LPF_CUTOFF_FREQ_last = LPF_CUTOFF_FREQ;
    }

    FlashSave((int)CalibrationSelect);  // Save calibration data

    Motor1_Velocity = (sensor1.getAngle() - Motor1_place_last) / 0.01f;
    Motor1_Velocity_f = Motor1_Velocity_filter(Motor1_Velocity);
    Motor1_place_last = sensor1.getAngle();

    Motor2_Velocity = -(sensor2.getAngle() - Motor2_place_last) / 0.01f;
    Motor2_Velocity_f = Motor2_Velocity_filter(Motor2_Velocity);
    Motor2_place_last = sensor2.getAngle();

    body.MotorVelocityF[0] = Motor1_Velocity_f;
    body.MotorVelocityF[1] = Motor2_Velocity_f;

    if ((SwitchUser == SWITCH_USER_MODE_SAMPLE_TORQUE_M1) && (Slot_calibration_mark == 0)) {
      Serial.print(" motor1 ");
      CalibrationCurrentSp(-sensor1.getAngle(), Motor1_Velocity_f, &motor1);
    }
    if ((SwitchUser == SWITCH_USER_MODE_SAMPLE_TORQUE_M2) && (Slot_calibration_mark == 0)) {
      Serial.print(" motor2 ");
      CalibrationCurrentSp(sensor2.getAngle(), Motor2_Velocity_f, &motor2);
    }

    float Rax[2];
    float Lax[2];
    float bodyH = 0.06f;
    float bodyRoll = BodyRoll_f;

    if (MasterSlaveSelection == MASTER_SLAVE_SELECTION_MASTER)  // Host mode
    {
      if ((pid_gains_mode == REMOTE_CONTROL_PID_GAINS_MODE_OFF) || (RobotTumble == ROBOT_TUMBLE_YES)) {
        if (Communication_object == COMMUNICATION_OBJECT_TWO_OR_FOUR_WHEEL_BALANCE && SwitchUser != SWITCH_USER_MODE_SAMPLE_TORQUE_M1 && SwitchUser != SWITCH_USER_MODE_SAMPLE_TORQUE_M2)  //
        {
          motor1.target = 0;
          motor2.target = 0;
        }

        bodyH = 0.06;
        bodyRoll = 0;
        BodyX = 0;
        bodyRoll = 0;
        BodyPitching_f = 0;

        Angle_Pid.integral = 0;
        Speed_Pid.integral = 0;
        Yaw_Pid.integral = 0;

        body.zo1 = 0;
        body.zo2 = 0;
        body.zo3 = 0;
        body.zo4 = 0;

        body.xo1 = 0;
        body.xo2 = 0;
        body.xo3 = 0;
        body.xo4 = 0;

        body_data_init();
      } else if ((pid_gains_mode_is_enabled(pid_gains_mode)) && (RobotTumble == ROBOT_TUMBLE_NO))  //
      {

        if (SwitchingPattern == SWITCHING_PATTERN_TWO_WHEEL_MODE)  // 2-wheel mode
        {
          PIDcontroller_posture(time_dt);  // PID controller

          body.zo1 = 0;
          body.zo2 = 0;
          body.zo3 = 0;
          body.zo4 = 0;

          body.xo1 = 0;
          body.xo2 = 0;
          body.xo3 = 0;
          body.xo4 = 0;

          if (roll_mode == REMOTE_CONTROL_ROLL_MODE_AUTO)
            bodyRoll = Roll_Pid.output;

          if (TargetLegLength == 0)
            bodyH = LegLength_f;
          else
            bodyH = TargetLegLength;
        } else if ((SwitchingPattern == SWITCHING_PATTERN_FOUR_WHEEL_MODE) && (MasterSlaveSelection == MASTER_SLAVE_SELECTION_MASTER))  // 4-wheel mode && Host mode
        {
          TrotGaitAlgorithm();  // Gait
          PIDcontroller_posture_4wheel(time_dt);

          Send_Serial1();  // Send data to slave
          motor1.target = body.MT[0];
          motor2.target = body.MT[1];

          bodyH = body.H_fron;

          bodyRoll = 0;
          BodyX = 0;
          bodyRoll = 0;
          BodyPitching_f = 0;
        }
      }
    } else  // Slave mode
    {

      bodyH = body.H_back;

      bodyRoll = 0;
      BodyX = 0;
      bodyRoll = 0;
      BodyPitching_f = 0;

      Send_Serial2();
      if (body.Serial1HZ >= 50) {

        body.xo2 = -body.xo4;
        body.xo1 = -body.xo3;
        body.zo2 = body.zo4;
        body.zo1 = body.zo3;

        motor1.target = body.MT[2];
        motor2.target = body.MT[3];
      } else {
        bodyH = 0.06;
        bodyRoll = 0;
        BodyX = 0;
        bodyRoll = 0;
        BodyPitching_f = 0;

        body.xo2 = 0;
        body.xo1 = 0;
        body.zo2 = 0;
        body.zo1 = 0;

        motor1.target = 0;
        motor2.target = 0;
      }
    }

    if (RobotTumble == ROBOT_TUMBLE_YES)  // Machine fall
    {
      bodyH = 0.06;
      bodyRoll = 0;
      BodyX = 0;
      bodyRoll = 0;
      BodyPitching_f = 0;
    }

    if (RightInverseKinematics(BarycenterX - BodyX + body.xo2, bodyH - bodyRoll - body.zo2, BodyPitching_f, Rax))
      Serial.println("RightInverseKinematics no");

    if (LeftInverseKinematics(BarycenterX - BodyX - body.xo1, bodyH + bodyRoll - body.zo1, BodyPitching_f, Lax))
      Serial.println("LeftInverseKinematics no");

    if (posture_or_mark_mode == REMOTE_CONTROL_PM_POSTURE_MODE)  // Posture
    {
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

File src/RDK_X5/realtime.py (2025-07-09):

import base64  # Used for Base64 encoding and decoding, and for encoding and transmitting audio data
import json  # Handling data exchange in JSON format
import os  # Operating system interface, used to read environment variables
import queue  # Thread-safe queue for microphone data buffering
import socket  # Network socket operations
import ssl
import subprocess  # Run external programs (e.g., open Notepad)
import threading  # Multithreading support
import time  # Time-related operations
import pyaudio  # Audio input and output processing
import socks  # SOCKS proxy support
import websocket  # WebSocket client
from dotenv import load_dotenv  # Load environment variables from.env file

import ES02_def_function

# Load the environment variable configuration from the.env file
load_dotenv()

# Set the SOCKS5 proxy (globally replace the socket implementation)
socket.socket = socks.socksocket

# Get the OpenAI API key from the environment variable
API_KEY = os.getenv("OPENAI_API_KEY")
if not API_KEY:
    raise ValueError("Please set the 'OPENAI_API_KEY' environment variable. The API key is missing.")

# WebSocket server URL (real-time voice conversion interface)
# WS_URL = 'wss://app-dev.easyone.ai:8815/api/realtime-convert'
WS_URL = 'wss://api.openai.com/v1/realtime?model=gpt-4o-mini-realtime-preview-2024-12-17'

# Audio stream parameter configuration
CHUNK_SIZE = 1024  # Size of each audio data chunk to process (bytes)
RATE = 24000  # Audio sampling rate (Hz)
FORMAT = pyaudio.paInt16  # Audio format (16-bit integer PCM)

# Global variable definitions
audio_buffer = bytearray()  # Store the received audio data (for speaker playback)
mic_queue = queue.Queue()  # Thread-safe queue for microphone collection data

stop_event = threading.Event()  # Thread stop event flag

mic_on_at = 0  # Microphone activation timestamp (for echo cancellation)
mic_active = None  # Current state record of the microphone
REENGAGE_DELAY_MS = 500  # Delay time to reactivate the microphone (milliseconds)


def clear_audio_buffer():
    """Clear the audio playback buffer"""
    global audio_buffer
    audio_buffer = bytearray()  # Reset to an empty byte array
    print('🔵 Audio buffer cleared')


def stop_audio_playback():
    """Stop audio playback (set the playback status flag)"""
    global is_playing
    is_playing = False
    print('🔵 Audio playback stopped')


def mic_callback(in_data, frame_count, time_info, status):
    """
    Microphone data collection callback function
    Parameters:
        in_data: Input audio data (binary)
        frame_count: Number of frames (number of audio frames in this callback)
        time_info: Time information dictionary
        status: Status flag (normal/error)
    Returns:
        (None, pyaudio.paContinue) indicating to continue collection
    """
    global mic_on_at, mic_active

    # Detect and update the microphone status
    if mic_active != True:
        print('🎙️🟢 Microphone activated')
        mic_active = True

    # Put the audio data into the queue (thread-safe)
    mic_queue.put(in_data)

    # Commented-out echo cancellation logic (can be enabled as needed)
    # if time.time() > mic_on_at:
    #     if mic_active != True:
    #         print('🎙️🟢 Microphone activated')
    #         mic_active = True
    #     mic_queue.put(in_data)
    # else:
    #     if mic_active != False:
    #         print('🎙️🔴 Microphone muted')
    #         mic_active = False

    return (None, pyaudio.paContinue)  # Return empty data and the flag to continue collection


def send_mic_audio_to_websocket(ws):
    """
    Send microphone audio data to the WebSocket server
    Parameters:
        ws: Established WebSocket connection object
    """
    try:
        while not stop_event.is_set():  # Keep running until a stop signal is received
            if not mic_queue.empty():  # Check if there is data in the queue
                # Get an audio data chunk from the queue
                mic_chunk = mic_queue.get()

                # Base64 encode the audio data (suitable for JSON transmission)
                encoded_chunk = base64.b64encode(mic_chunk).decode('utf-8')

                # Construct a WebSocket message (JSON format)
                message = json.dumps({
                    'type': 'input_audio_buffer.append',  # Message type
                    'audio': encoded_chunk  # Encoded audio data
                })

                try:
                    ws.send(message)  # Send the message
                except Exception as e:
                    print(f'Error sending microphone audio: {e}')
    except Exception as e:
        print(f'Exception in the microphone data sending thread: {e}')
    finally:
        print('Microphone data sending thread exited')


def speaker_callback(in_data, frame_count, time_info, status):
    """
    Speaker playback callback function
    Parameters:
        in_data: Input data (not used)
        frame_count: Number of audio frames required
        time_info: Time information dictionary
        status: Status flag
    Returns:
        (audio_chunk, pyaudio.paContinue) audio data and the flag to continue playback
    """
    global audio_buffer, mic_on_at

    # Calculate the number of bytes needed (16-bit audio = 2 bytes/sample)
    bytes_needed = frame_count * 2
    current_buffer_size = len(audio_buffer)

    if current_buffer_size >= bytes_needed:
        # The buffer has enough data: take out the required data
        audio_chunk = bytes(audio_buffer[:bytes_needed])
        audio_buffer = audio_buffer[bytes_needed:]  # Update the buffer

        # Set the microphone activation time (current time + delay) to avoid echo
        mic_on_at = time.time() + REENGAGE_DELAY_MS / 1000
    else:
        # The buffer is insufficient: fill the remaining part with silent data
        audio_chunk = bytes(audio_buffer) + b'\x00' * (bytes_needed - current_buffer_size)
        audio_buffer.clear()  # Clear the buffer

    return (audio_chunk, pyaudio.paContinue)
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

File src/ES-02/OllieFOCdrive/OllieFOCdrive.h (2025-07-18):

#ifndef OllieFOCdrive_h
#define OllieFOCdrive_h

#include <Arduino.h>
#include "filter.h"
#include "touchscreen.h"

#define SWITCHING_PATTERN_TWO_WHEEL_MODE 0  // Self-balancing two-wheel mode
#define SWITCHING_PATTERN_FOUR_WHEEL_MODE 1 // Four-legged walking mode

#define MASTER_SLAVE_SELECTION_SLAVE 0  // The controller is a slave
#define MASTER_SLAVE_SELECTION_MASTER 1 // The controller is the master

#define ADJUSTMENT_PARAM_BALANCE_SPEED_YAW_ROLL 0
#define ADJUSTMENT_PARAM_BALL_PUSHING 1 // For tuning main balance and movement PID loops

#define SWITCH_USER_MODE_VIEW_ENCODER 0     // View encoder position and direction
#define SWITCH_USER_MODE_SAMPLE_TORQUE_M1 1 // Sample motor 1 torque compensation data
#define SWITCH_USER_MODE_SAMPLE_TORQUE_M2 2 // Sample motor 2 torque compensation data
#define SWITCH_USER_MODE_TORQUE_MODE 3      // Direct torque control mode
#define SWITCH_USER_MODE_SPEED_MODE 4       // Speed control mode
#define SWITCH_USER_MODE_ANGLE_MODE 5       // Angle control mode

#define TORQUE_COMPENSATION_OFF 0 // Torque compensation is off
#define TORQUE_COMPENSATION_ON 1  // Torque compensation is on

#define COMMUNICATION_OBJECT_TWO_OR_FOUR_WHEEL_BALANCE 0 // Two-wheel balance mode
#define COMMUNICATION_OBJECT_SIMPLEFOC_STUDIO 1          // SimpleFOC Studio host computer
#define COMMUNICATION_OBJECT_CONTROL_DUAL_MOTORS 2       // Control dual motors
#define COMMUNICATION_OBJECT_SAMPLE_TORQUE_DATA 3        // Sample torque data

#define ROBOT_TUMBLE_NO 0  // Robot is not tumbling
#define ROBOT_TUMBLE_YES 1 // Robot is tumbling

#define SENSOR_SWITCH_SPI 1
#define SENSOR_SWITCH_IIC_AS5600 2

#define CURRENT_LOOP_OFF 0 // Current loop is off
#define CURRENT_LOOP_ON 1  // Current loop is on

#define REMOTE_CONTROL_PID_GAINS_MODE_OFF 0
#define REMOTE_CONTROL_PID_GAINS_MODE_ON_WITHOUT_TOUCH 1
#define REMOTE_CONTROL_PID_GAINS_MODE_ON_WITH_TOUCH 2

#define REMOTE_CONTROL_PM_POSTURE_MODE 0 // Posture control mode
#define REMOTE_CONTROL_PM_MARK_MODE 1    // Mark control mode

#define REMOTE_CONTROL_ROLL_MODE_MANUAL 0
#define REMOTE_CONTROL_ROLL_MODE_AUTO 1

#define REMOTE_CONTROL_ATTITUDE_MODE_DEFAULT 0
#define REMOTE_CONTROL_ATTITUDE_MODE_PITCHING_ADJUST 1 // Pitching adjustment mode
#define REMOTE_CONTROL_ATTITUDE_MODE_BALL_POISE 2      // Ball poise mode

typedef struct
{
  unsigned char rxbuf[30];//Receive data buffer
  unsigned char txbuf[30];
  unsigned char recstatu;//Indicates whether in a state of receiving data packet
  unsigned char count;//Counter
  unsigned char packerflag;//Flag indicating whether a complete data packet is received
  unsigned char dat;     
} Serial_t;


typedef struct
{
  // Gait parameters
  //float stepSize;   // Angle change per step
  
  float delayTime;  // Delay time per step
  //float cycleSteps; // Time for one cycle
  float CurrentSteps; //Current step count
  float xt;       // Target position
  float xs1;       // Start position
  float xf1;       // End position  
  float xs2;       // Start position
  float xf2;       // End position
  float xs3;       // Start position
  float xf3;       // End position  
  float xs4;       // Start position
  float xf4;       // End position  
  float h;        // Maximum height  
  float H_fron;  //     
  float H_back;  //   
  float H_R;  //     
  float H_P;  //  
  float zs;       // Start height
  float lambda[2];   // λ parameter
  float sigma;
  float Ts;       // Period

  float xo1;       // x1 output position
  float zo1;        //Output maximum height

  float xo2;       // x2 output position
  float zo2;        //Output maximum height

  float xo3;       // x3 output position
  float zo3;        //Output maximum height

  float xo4;       // x4 output position
  float zo4;        //Output maximum height  

  float MT[4];   //Motor target values

  float MotorVelocityF[4];   //Motor velocity


  uint8_t MotorMode;   //Motor working mode

  int Serial1HZ;
  int Serial1count;

  float BodyRoll4Wheel;
  float BodyPitching4Wheel;
  float BodyPitching4WheelT;
  float BodyPitching4WheelTF;
      
} body_t;


typedef union 
{
  struct 
  {
    float x;
    float y;
    float z;
  };
  float axis[3];
} Axis3f;
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

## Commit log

2025-07-09 Init project
    [BOM.xlsx, loamcake.stl, lowercover.stl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]
2025-12-18 BOM update, pcb complete
    [BOM.xlsx]
2026-03-26 Newly added Bluetooth control
    Now, you can control it using Bluetooth instead of the model remote control. When connected via Bluetooth, use Bluetooth data; when not connected, use the sbus input.
    [loamcake.stl]
2026-04-23 Fine-tuning the model and PID modification
    [Calf_Inside.stl, Calf_Outside.stl, Thigh_L.stl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]
